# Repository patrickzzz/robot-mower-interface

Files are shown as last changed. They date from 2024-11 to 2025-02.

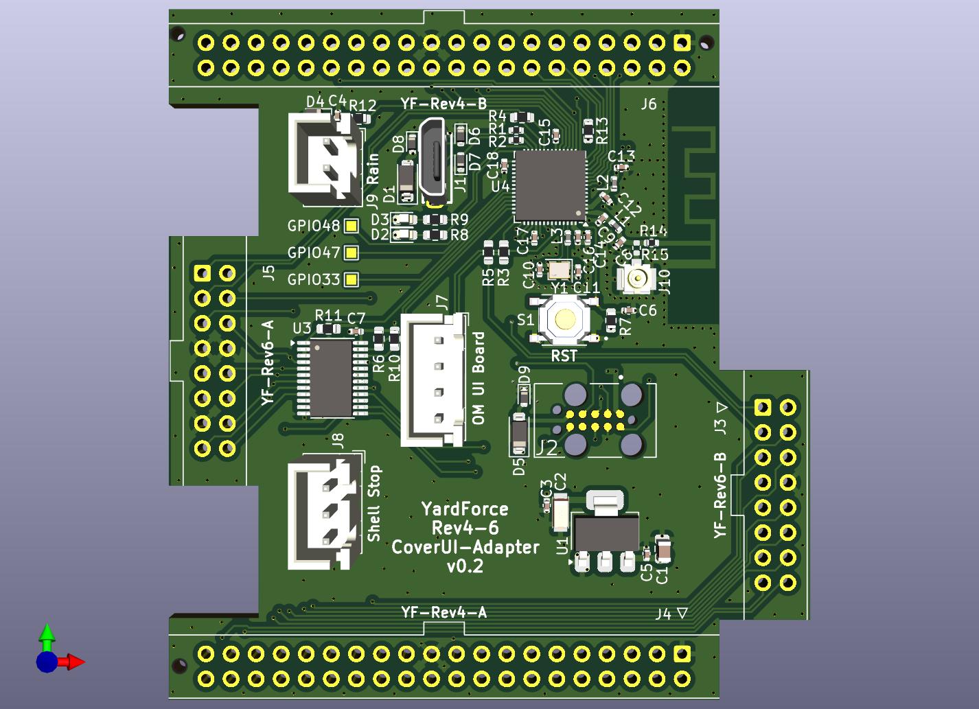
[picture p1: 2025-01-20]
hardware/yardforce/YF-Rev4-6-Adapter.jpg

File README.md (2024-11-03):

# Robot Mower Interface

## Overview
This project provides an interface for controlling and managing a robot mower.

Initially this is done for a Ferrex R800Easy+ robot mower (meaning, it will be probably easily adaptable to other models from Ferrex, Yard Force (Yardforce), Garden Feelings and so on). 

## Original Goals
- The mower lacks the possibility to mow less than 4 hours a day. Also it has no app to control it (other models may have an app, but only closed source). These are the main reasons for this project.
- The main goal is a personal use case. There still might be errors in the project and/or in the documentation.

## Features
- **Control**: Execute Start, Home, Stop, and Lock on the mower.
- **Configuration**: Configure Wi-Fi settings (either connected to a Wifi, or as Access Point).
- **Scheduling**: Set mowing schedules.
- **Status**: View mower status
- **Logs**: See logs from the mower
- **API** Access all features via API
- **Web Interface** Access all features via a web interface
- **OTA Updates** Update the firmware and filesystem of the mower interface over the air (OTA) in Webinterface or API Endpoint.

## Demo of first running version
Demo (https://www.youtube.com/watch?v=VGW71knz1Dk)

## License
This project is licensed under the Creative Commons Zero v1.0 Universal (CC0 1.0) - see the [LICENSE](LICENSE) file for details.

It's important to note that the original firmware of the mower is not open source, and this project is not affiliated with the manufacturer.
The original firmware of the mower is not changed in any way, but the warranty of the mower will be voided modifying the mower in this way.
I am not responsible for any damage to the mower or any other device.

## API Endpoint Documentation

### 1. `/start`
- **Method:** `POST`
- **Description:** Starts the mower.
- **Parameters:** None
- **Response:** `200 OK` if successful

### 2. `/home`
- **Method:** `POST`
- **Description:** Sends the mower back to the charging station.
- **Parameters:** None
- **Response:** `200 OK` if successful

### 3. `/stop`
- **Method:** `POST`
- **Description:** Stops the mower.
- **Parameters:** None
- **Response:** `200 OK` if successful

### 4. `/lock`
- **Method:** `POST`
- **Description:** Locks the mower.
- **Parameters:** None
- **Response:** `200 OK` if successful

### 5. `/unlock`
- **Method:** `POST`
- **Description:** Unlocks the mower.
- **Parameters:** None
- **Response:** `200 OK` if successful

### 6. `/status`
- **Method:** `GET`
- **Description:** Returns the current status of the mower.
- **Parameters:** None
- **Response:** JSON object with the following fields:
    - `date`: Current date on the mower
    - `time`: Current time on the mower
    - `isCharging`: Charging status
    - `isLocked`: Lock status
    - `isEmergency`: Emergency status
    - `isIdle`: Idle status
    - `isAccessPoint`: Access Point mode status
    - `hostname`: Hostname of the mower
    - `ssid`: Current WiFi SSID
    - `ip`: IP address of the mower
    - `mowingPlanActive`: Indicates if the mowing plan is active

### 7. `/mowing-plan`
- **Method:** `GET`
- **Description:** Retrieves the current mowing plan.
- **Parameters:** None
- **Response:** JSON file of the mowing plan if exists, or `204 No Content` if not found

### 8. `/mowing-plan`
- **Method:** `POST`
- **Description:** Sets a new mowing plan.
- **Payload:** JSON object with the following fields:
    - `customMowingPlanActive` (boolean): Activates or deactivates the custom mowing plan
    - `days` (array of booleans): Specifies active days (Mon-Sun)
    - `planTimeStart` (string): Mowing start time (e.g., `"09:00"`)
    - `planTimeEnd` (string): Mowing end time (e.g., `"17:00"`)
- **Response:** `200 OK` if successful, `400 Bad Request` if parameters are missing

### 9. `/wifis`
- **Method:** `GET`
- **Description:** Returns a list of available WiFi networks.
- **Parameters:** None
- **Response:** JSON array with SSIDs of the detected networks

### 10. `/wifi`
- **Method:** `POST`
- **Description:** Sets the WiFi credentials for the mower to connect to.
- **Payload:** JSON object with the following fields:
    - `ssid` (string): WiFi SSID
    - `password` (string): WiFi password
- **Response:** `200 OK` if successful, `400 Bad Request` if parameters are missing

### 11. `/date-time`
- **Method:** `POST`
- **Description:** Sets the date and time on the mower.
- **Payload:** JSON object with the following fields:
    - `date` (string): Date in the format `YYYY-MM-DD`
    - `time` (string): Time in the format `HH:MM`
- **Response:** `200 OK` if successful, `400 Bad Request` if parameters are missing

### 12. `/update`
- **Method:** `POST`
- **Description:** Allows for simultaneous upload and update of both firmware and filesystem files on the device. This endpoint manages both types of updates, determining the file type based on the filename.
- **Payload:** Multipart form-data with up to two files:
  - `firmware.bin`: Firmware binary file for updating the main program.
  - `filesystem.bin`: Filesystem binary file (e.g., SPIFFS) for updating the file system.
- **Response:**
  - **`200 OK`**: Returns `"Update Success!"` if the upload and update process are successful for both files.
  - **`500 Internal Server Error`**: Returns `"Update Failed!"` if an error occurs during either update.
- **Usage Notes:**
  - **File Recognition**: The update type is determined by the filename—`firmware.bin` for firmware updates and `filesystem.bin` for filesystem updates.
  - **Restart**: Upon successful updates, the device automatically restarts to apply changes.

## Needed parts
- Ferrex R800Easy+ robot mower (or similar)
- ESP32 (e.g., ESP32 DevKitC)
- USB cable
- DC-DC step-down converter (~32V -> 5V)

## Software Installation Instructions
Follow these steps to install the mower control software on your ESP32:

- **Connect** your ESP32 to your computer via USB.
- **Clone** this Repository
- **Install** PlatformIO (if not installed)
- **Upload the File System:** In the project/backend directory, upload the filesystem to the ESP32 by running:
  ```bash
  pio run --target uploadfs
  ```
- **Upload the Firmware:** In the project/backend directory, upload the firmware to the ESP32:
  ```bash
  pio run --target upload
  ```

- **Verify Installation:** Once complete, the ESP32 should be ready to run with the mower control software, creating a Wifi Access Point with SSID "Robot Mower" and password: "MowerInterface".
- **While still connected with USB to the ESP32, open a Serial Monitor** and you should see the IP address of the ESP32. Use this IP address to access the web interface.
  ```bash
  pio device monitor
  ```

## Hardware Installation Instructions
- For now the ESP32 has to be powered from the mainboard, and several pins of the ESP32 have to be connected to the Cover-User-Interface-Board (CoverUI).
- The power (24V) will come from red J18 connector. This is constant and is not powered down in idle mode. Connect it to the DC-DC step-down converter and set this to 5V.
- The ESP32 will be powered from the 5V output of the DC-DC step-down converter.
- The Stop1 (J8) cable on the main board for now has to be disconnected. The bottom Stop button of the mower will not work anymore. The top Stop button will still work.
- The connection of the pins of the ESP32 will for now not be described here, but hopefully can be seen in the following pictures, or derived from the code.

## Photos





## Thanks To
Special thanks to the following projects and contributors:
- **[apehaenger/CoverUI](https://github.com/apehaenger/CoverUI)** — for extensive help on the mower and detailed documentation.
- **[ClemensElflein/OpenMower](https://github.com/ClemensElflein/OpenMower)** — for the inspiration behind this project.
- **[cedbossneo/Mowgli](https://github.com/cedbossneo/Mowgli)** — for mainboard documentation and insights.

And a big thanks to all contributors from these projects, as well as the developers of the hardware and software used in this project.

Last but not least, to my girlfriend and family for their patience and support during my development time.

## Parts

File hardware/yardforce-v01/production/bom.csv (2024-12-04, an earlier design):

Designator | Footprint | Quantity | Value | LCSC Part #
C1, C2 | 0603 | 2 | 10uF | C19702
C10, C11 | 0402 | 2 | 10pF | C32949
C12, C15, C16, C17, C18, C3, C4, C7 | 0402 | 8 | .1uF | C1525
C14, C6 | 0402 | 2 | 1uF | C52923
C9 | 0402 | 1 | 0.8pF | C5448872
D1 | D_SOD-123 | 1 | D_Schottky | C82288
D2 | 0603 | 1 | LED GREEN | C12624
D3 | 0603 | 1 | LED RED | C2286
D4 | D_SOD-323 | 1 | PDZ3.3B,115 | C426855
J1 | USB_Micro-B_Wuerth_614105150721_Vertical | 1 | USB_OTG | C668588
J7 | JST_XH_B4B-XH-A_1x04_P2.50mm_Vertical | 1 | OM UI Board | C144395
J8 | JST_XH_B3B-XH-A_1x03_P2.50mm_Vertical | 1 | Shell Stop | C144394
J9 | JST_XH_B2B-XH-A_1x02_P2.50mm_Vertical | 1 | Rain | C2910525
L1 | 0402 | 1 | 3.9nH | C370223
L2 | 0402 | 1 | 2.0nH | C963978
L3 | 0402 | 1 | 24nH | C401493
R1, R2 | 0402 | 2 | 0 | C17168
R10, R11, R12, R6, R7 | 0603 | 5 | 10k | C25804
R3, R4, R5 | 0603 | 3 | 22 | C23345
R8 | 0603 | 1 | 200 | C8218
R9 | 0603 | 1 | 220 | C22962
S1 | SW_TS-1187A-B-A-B | 1 | RST | C318884
U1 | SOT-223-3_TabPin2 | 1 | AMS1117-3.3 | C6186
U3 | TSSOP-24_4.4x7.8mm_P0.65mm | 1 | TCA9555PWR | C465732
U4 | QFN-56-1EP_7x7mm_P0.4mm_EP4x4mm_ThermalVias | 1 | ESP32-S3-FH4R2 | C3013940
Y1 | Crystal_SMD_2016-4Pin_2.0x1.6mm | 1 | 40MHz 10.5pF ±10ppm | C18209006

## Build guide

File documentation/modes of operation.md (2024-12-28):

## Possible operation modes

### Mainboard / CoverUI matrix of possible adapter connection variants

| Mainboard \ CoverUI | YF-Rev4-A\|B | YF-Rev6-A<br>via UART1[^1] | YF-Rev6-B<br>via UART2[^2] |
|---|:---:|:---:|:---:|
| **OM UI Board**<br>via UART0[^3] | ✔ | ✔ | ✔ |
| **YF-Rev4-A\|B**<br>No UART, read LED states  | ✔ | ✔ | ✔ |
| **YF-Rev6-A**<br>via UART1[^1] | ✔ | ✘ | ✔ |
| **YF-Rev6-B**<br>via UART2[^2] | ✔ | ✔ | ✘ |

[^1]: UART1 via TXD1 = GPIO17, RXD1 = GPIO18
[^2]: UART2 via TXDX = GPIO37, RXDX = GPIO38
[^3]: UART0 via TXD0 = GPIO43, RXD0 = GPIO44

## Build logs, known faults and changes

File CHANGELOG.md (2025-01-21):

# Changelog

All notable changes to this project are documented in this file.

## [0.3.2]
### Changed
- Don't truncate logs on every startup

### Fixed
- Correct loading of mowing plan on boot up

## [0.3.1]
### Changed
- Visualize Log message in webinterface as mono spaced text
- Load mowing plan on boot up again

## [0.3.0]
### Added
- Ability to update the firmware+filesystem of the mower interface over the air (OTA) in Webinterface or API Endpoint.

## [0.2.2]
### Added
- Automatically reconnect to Wifi if connection is lost

## [0.2.1]
### Changed
- Forced serving of html+js gzipped
- Increased wdt to 60s for handling bigger requests (hopefully not needed)

## [0.2.0]
### Added
- Documentation added.

### Changed
- Changed license from MIT to CC0 1.0 Universal.
- Minor improvements in frontend.
- Backend code restructuring.
- WiFi scanning now asynchronous.

### Fixed
- Issue with logging (log file truncation error corrected).
- Time setting now expects new JSON payload.

## [0.1.0]
### Initial Release
- Initial version of the project.

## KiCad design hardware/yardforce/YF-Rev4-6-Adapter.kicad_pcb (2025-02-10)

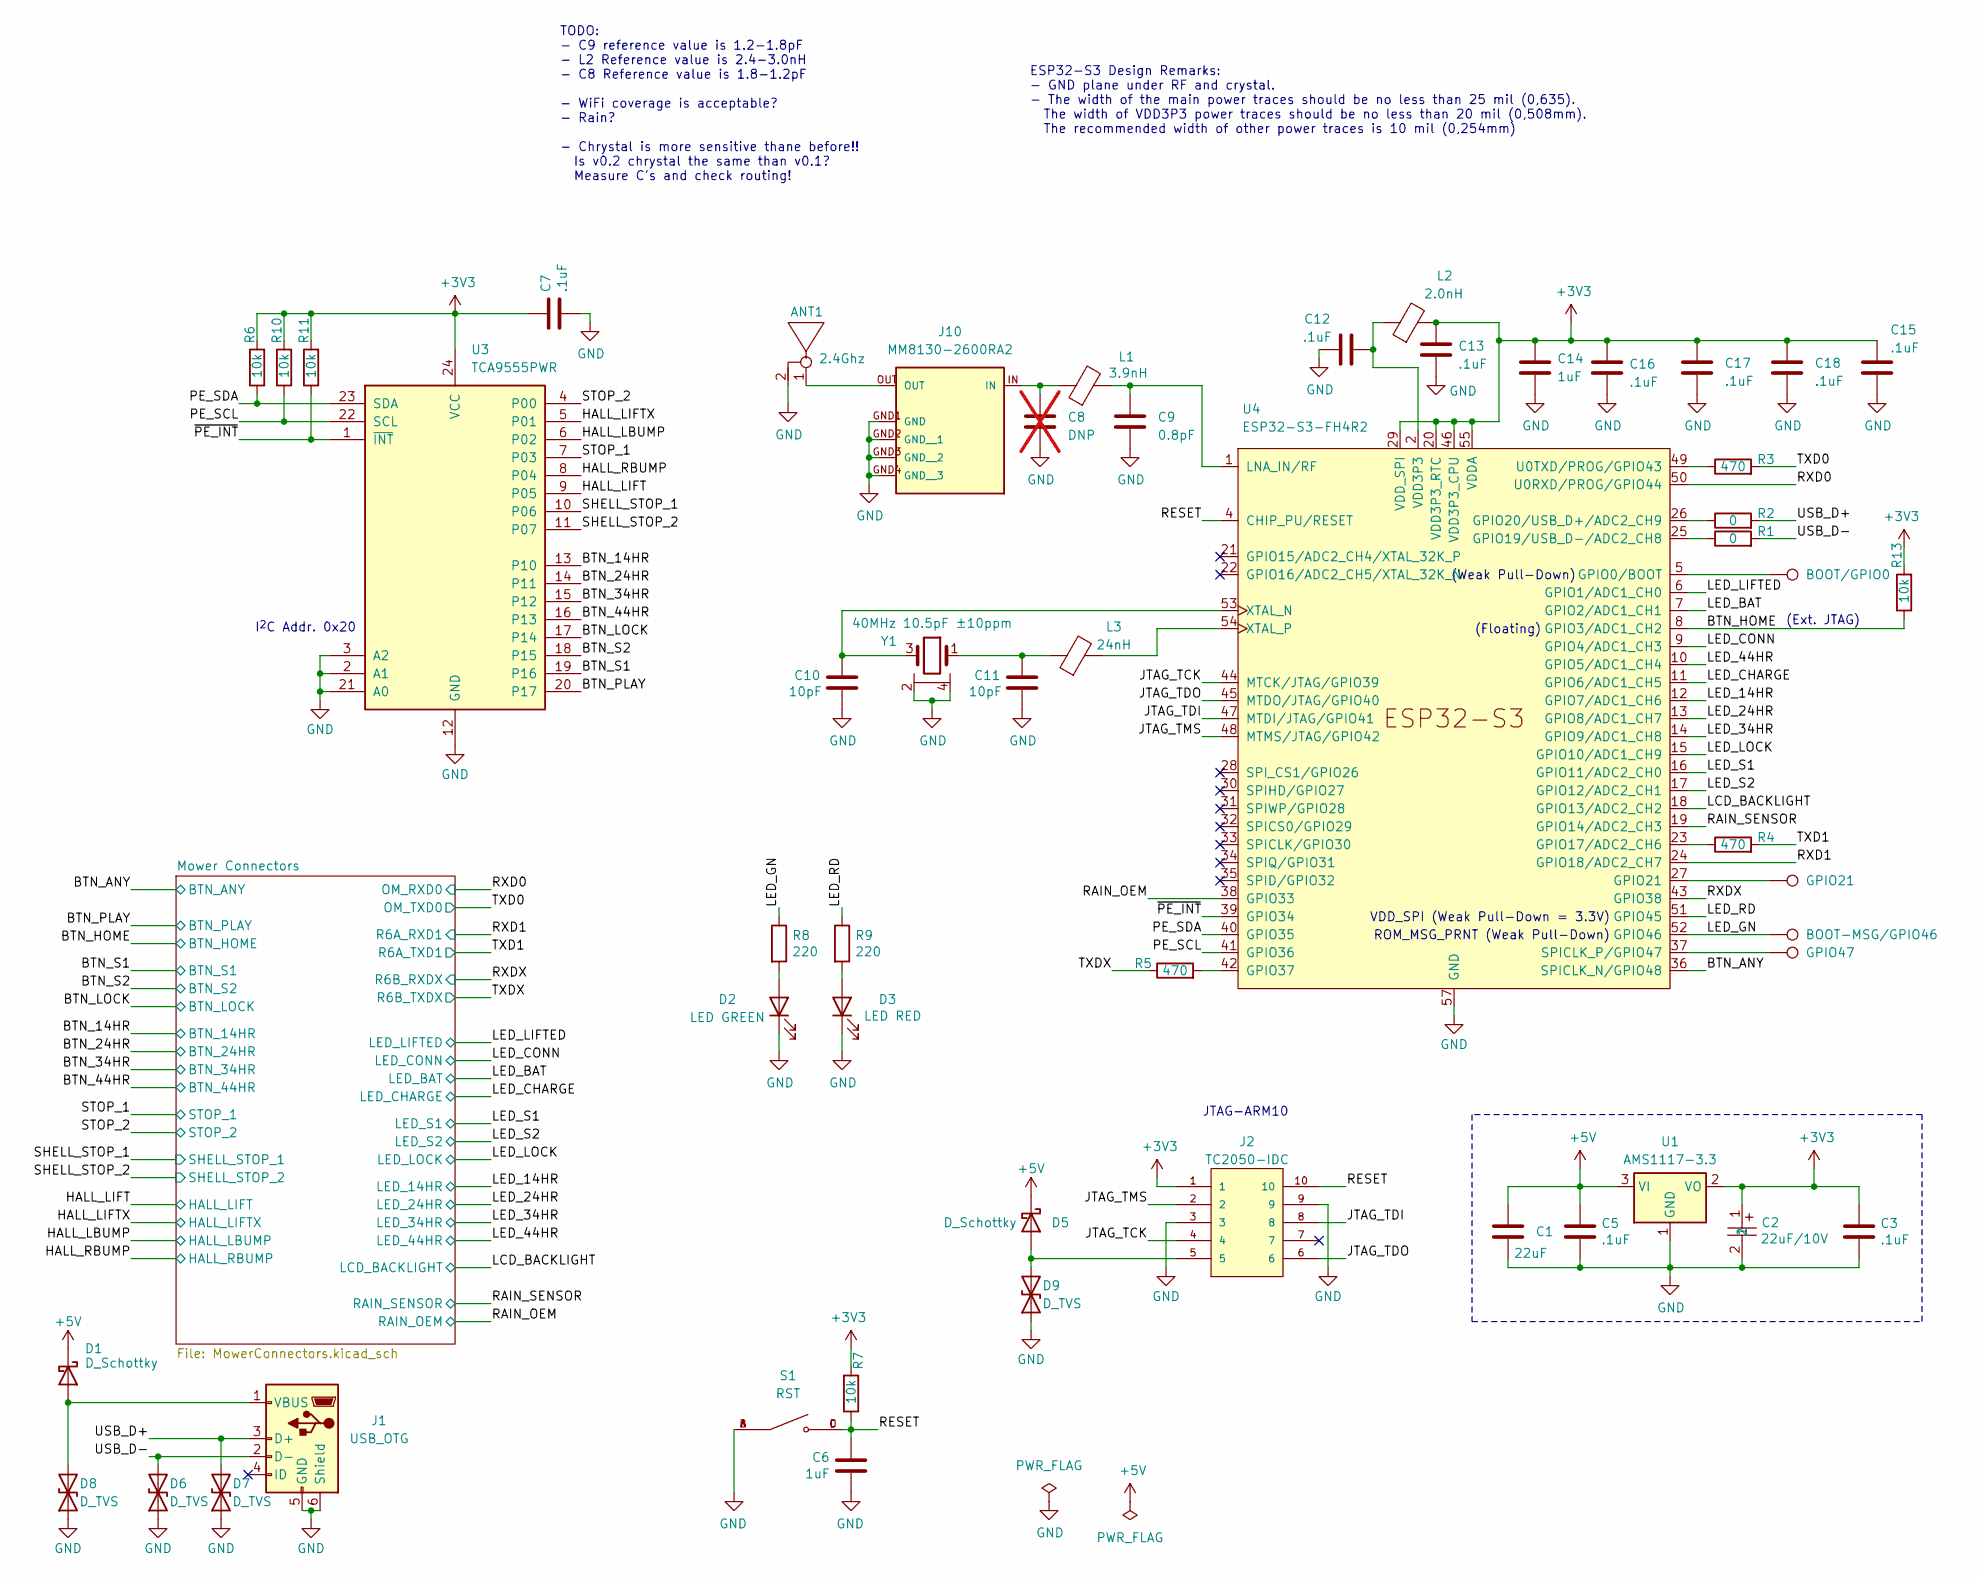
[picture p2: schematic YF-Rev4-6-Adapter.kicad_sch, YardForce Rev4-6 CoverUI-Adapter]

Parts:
ANT1: 2.4Ghz; PCB_Antenna_2.4GHz_Left
BOOT-MSG/GPIO46: TestPoint; TestPoint_Pad_1.0x1.0mm
BOOT/GPIO0: TestPoint; TestPoint_Pad_1.0x1.0mm
C1: 22uF; C_0805_2012Metric; LCSC C45783
C2: 22uF/10V; CASE-A_3216; LCSC C129272
C3, C5, C7, C12, C13, C15, C16, C17, C18: .1uF; C_0402_1005Metric; LCSC C1525
C6, C14: 1uF; C_0402_1005Metric; LCSC C52923
C8: DNP; C_0402_1005Metric; not fitted
C9: 0.8pF; C_0402_1005Metric; LCSC C5448872
C10, C11: 10pF; C_0402_1005Metric; MFR Part 0402CG140J500NT; LCSC C32949
D1, D5: D_Schottky; D_SOD-123; Part Number 1N5819HW-7-F; LCSC C82544
D2: LED GREEN; LED_0603_1608Metric; Part Number LTST-C191KGKT; Digikey 160-1446-1-ND
D3: LED RED; LED_0603_1608Metric; Part Number LTST-C191KRKT; Digikey 160-1447-1-ND
D6, D7, D8, D9: D_TVS; D_SOD-523; Part-Nr LESD5D5.0CT1G; LCSC C5449097
GPIO21, GPIO47: TestPoint; TestPoint_Pad_1.0x1.0mm
J1: USB_OTG; MINI-USB-SMD_U255-051N-4BH70-XS; LCSC C437033
J2: TC2050-IDC; TAG-CONNECT_TC2050-IDC; PARTREV A
J10: MM8130-2600RA2; MURATA_MM8130-2600RA2; LCSC C91633
L1: 3.9nH; L_0402_1005Metric; LCSC C370223
L2: 2.0nH; L_0402_1005Metric; LCSC C963978
L3: 24nH; L_0402_1005Metric; MFR Part SDCL1005C24NJTDF; LCSC C401493
R1, R2: 0; R_0402_1005Metric; LCSC C17168
R3, R4, R5: 470; R_0603_1608Metric; LCSC C23179
R6, R7, R10, R11, R13: 10k; R_0603_1608Metric; LCSC C25804
R8, R9: 220; R_0603_1608Metric; LCSC C22962
S1: RST; SW_TS-1187A-B-A-B; PARTREV A0; LCSC C318884
U1: AMS1117-3.3; SOT-223-3_TabPin2; LCSC C6186
U3: TCA9555PWR; TSSOP-24_4.4x7.8mm_P0.65mm; LCSC C465732
U4: ESP32-S3-FH4R2; QFN-56-1EP_7x7mm_P0.4mm_EP4x4mm_ThermalVias; LCSC C3013940
Y1: 40MHz 10.5pF ±10ppm; Crystal_SMD_2016-4Pin_2.0x1.6mm; MF Part K2B4000010510; LCSC C18209006

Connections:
+3V3: C2.1, C3.1, C7.1, C13.1, C14.1, C15.1, C16.1, C17.1, C18.1, J2.1, L2.2, R6.2, R7.2, R10.2, R11.2, R13.2, U1.2 (VO), U3.24 (VCC), U4.20 (VDD3P3_RTC), U4.29 (VDD_SPI), U4.46 (VDD3P3_CPU), U4.55 (VDDA), U4.56 (VDDA); also elsewhere on the board
+5V: C1.1, C5.1, D1.1 (K), D5.1 (K), U1.3 (VI); also elsewhere on the board
/BTN_14HR: U3.13 (P10); also elsewhere on the board
/BTN_24HR: U3.14 (P11); also elsewhere on the board
/BTN_34HR: U3.15 (P12); also elsewhere on the board
/BTN_44HR: U3.16 (P13); also elsewhere on the board
/BTN_ANY: U4.36 (SPICLK_N/GPIO48); also elsewhere on the board
/BTN_HOME: R13.1, U4.8 (GPIO3/ADC1_CH2); also elsewhere on the board
/BTN_LOCK: U3.17 (P14); also elsewhere on the board
/BTN_PLAY: U3.20 (P17); also elsewhere on the board
/BTN_S1: U3.19 (P16); also elsewhere on the board
/BTN_S2: U3.18 (P15); also elsewhere on the board
/HALL_LBUMP: U3.6 (P02); also elsewhere on the board
/HALL_LIFT: U3.9 (P05); also elsewhere on the board
/HALL_LIFTX: U3.5 (P01); also elsewhere on the board
/HALL_RBUMP: U3.8 (P04); also elsewhere on the board
/JTAG_TCK: J2.4, U4.44 (MTCK/JTAG/GPIO39)
/JTAG_TDI: J2.8, U4.47 (MTDI/JTAG/GPIO41)
/JTAG_TDO: J2.6, U4.45 (MTDO/JTAG/GPIO40)
/JTAG_TMS: J2.2, U4.48 (MTMS/JTAG/GPIO42)
/LCD_BACKLIGHT: U4.18 (GPIO13/ADC2_CH2); also elsewhere on the board
/LED_14HR: U4.12 (GPIO7/ADC1_CH6); also elsewhere on the board
/LED_24HR: U4.13 (GPIO8/ADC1_CH7); also elsewhere on the board
/LED_34HR: U4.14 (GPIO9/ADC1_CH8); also elsewhere on the board
/LED_44HR: U4.10 (GPIO5/ADC1_CH4); also elsewhere on the board
/LED_BAT: U4.7 (GPIO2/ADC1_CH1); also elsewhere on the board
/LED_CHARGE: U4.11 (GPIO6/ADC1_CH5); also elsewhere on the board
/LED_CONN: U4.9 (GPIO4/ADC1_CH3); also elsewhere on the board
/LED_GN: BOOT-MSG/GPIO46.1, R8.1, U4.52 (GPIO46)
/LED_LIFTED: U4.6 (GPIO1/ADC1_CH0); also elsewhere on the board
/LED_LOCK: U4.15 (GPIO10/ADC1_CH9); also elsewhere on the board
/LED_RD: R9.1, U4.51 (GPIO45)
/LED_S1: U4.16 (GPIO11/ADC2_CH0); also elsewhere on the board
/LED_S2: U4.17 (GPIO12/ADC2_CH1); also elsewhere on the board
/PE_SCL: R10.1, U3.22 (SCL), U4.41 (GPIO36)
/PE_SDA: R6.1, U3.23 (SDA), U4.40 (GPIO35)
/RAIN_OEM: U4.38 (GPIO33); also elsewhere on the board
/RAIN_SENSOR: U4.19 (GPIO14/ADC2_CH3); also elsewhere on the board
/RESET: C6.1, J2.10, R7.1, S1.C, S1.D, U4.4 (CHIP_PU/RESET)
/RXD0: U4.50 (U0RXD/PROG/GPIO44); also elsewhere on the board
/RXD1: U4.24 (GPIO18/ADC2_CH7); also elsewhere on the board
/RXDX: U4.43 (GPIO38); also elsewhere on the board
/SHELL_STOP_1: U3.10 (P06); also elsewhere on the board
/SHELL_STOP_2: U3.11 (P07); also elsewhere on the board
/STOP_1: U3.7 (P03); also elsewhere on the board
/STOP_2: U3.4 (P00); also elsewhere on the board
/TXD0: R3.2; also elsewhere on the board
/TXD1: R4.2; also elsewhere on the board
/TXDX: R5.1; also elsewhere on the board
/USB_D+: D7.2 (A2), J1.3 (D+), R2.2
/USB_D-: D6.2 (A2), J1.2 (D-), R1.2
/~PE_INT: R11.1, U3.1 (~INT), U4.39 (GPIO34)
GND: ANT1.2, C1.2, C2.2, C3.2, C5.2, C6.2, C7.2, C8.2, C9.2, C10.2, C11.2, C12.1, C13.2, C14.2, C15.2, C16.2, C17.2, C18.2, D2.1 (K), D3.1 (K), D6.1 (A1), D7.1 (A1), D8.1 (A1), D9.1 (A1), J1.5 (GND), J1.6 (Shield), J2.3, J2.9, J10.GND1 (GND), J10.GND2 (GND__1), J10.GND3 (GND__2), J10.GND4 (GND__3), S1.A, S1.B, U1.1 (GND), U3.2 (A1), U3.3 (A2), U3.12 (GND), U3.21 (A0), U4.57 (GND), Y1.2, Y1.4; also elsewhere on the board
unnamed: ANT1.1, J10.OUT
unnamed: C8.1, J10.IN, L1.1
unnamed: C11.1, L3.1, Y1.1
unnamed: D1.2 (A), D8.2 (A2), J1.1 (VBUS)
unnamed: D2.2 (A), R8.2
unnamed: D3.2 (A), R9.2
unnamed: D5.2 (A), D9.2 (A2), J2.5
unnamed: BOOT/GPIO0.1, U4.5 (GPIO0/BOOT)
unnamed: R4.1, U4.23 (GPIO17/ADC2_CH6)
unnamed: R1.1, U4.25 (GPIO19/USB_D-/ADC2_CH8)
unnamed: R2.1, U4.26 (GPIO20/USB_D+/ADC2_CH9)
unnamed: GPIO21.1, U4.27 (GPIO21)
unnamed: R5.2, U4.42 (GPIO37)
unnamed: C9.1, L1.2, U4.1 (LNA_IN/RF)
unnamed: GPIO47.1, U4.37 (SPICLK_P/GPIO47)
unnamed: R3.1, U4.49 (U0TXD/PROG/GPIO43)
unnamed: C10.1, U4.53 (XTAL_N), Y1.3
unnamed: L3.2, U4.54 (XTAL_P)
VDD3P3: C12.2, L2.1, U4.2 (VDD3P3), U4.3 (VDD3P3)

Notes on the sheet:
(Floating)
ESP32-S3 Design Remarks: - GND plane under RF and crystal. - The width of the main power traces should be no less than 25 mil (0,635). The width of VDD3P3 power traces should be no less than 20 mil (0,508mm). The recommended width of other power traces is 10 mil (0,254mm)
ROM_MSG_PRNT (Weak Pull-Down)
(Weak Pull-Down)
JTAG-ARM10
(Ext. JTAG)
VDD_SPI (Weak Pull-Down = 3.3V)
I^{2}C Addr. 0x20
TODO: - C9 reference value is 1.2-1.8pF - L2 Reference value is 2.4-3.0nH - C8 Reference value is 1.8-1.2pF - WiFi coverage is acceptable? - Rain? - Chrystal is more sensitive thane before!! Is v0.2 chrystal the same than v0.1? Measure C's and check routing!

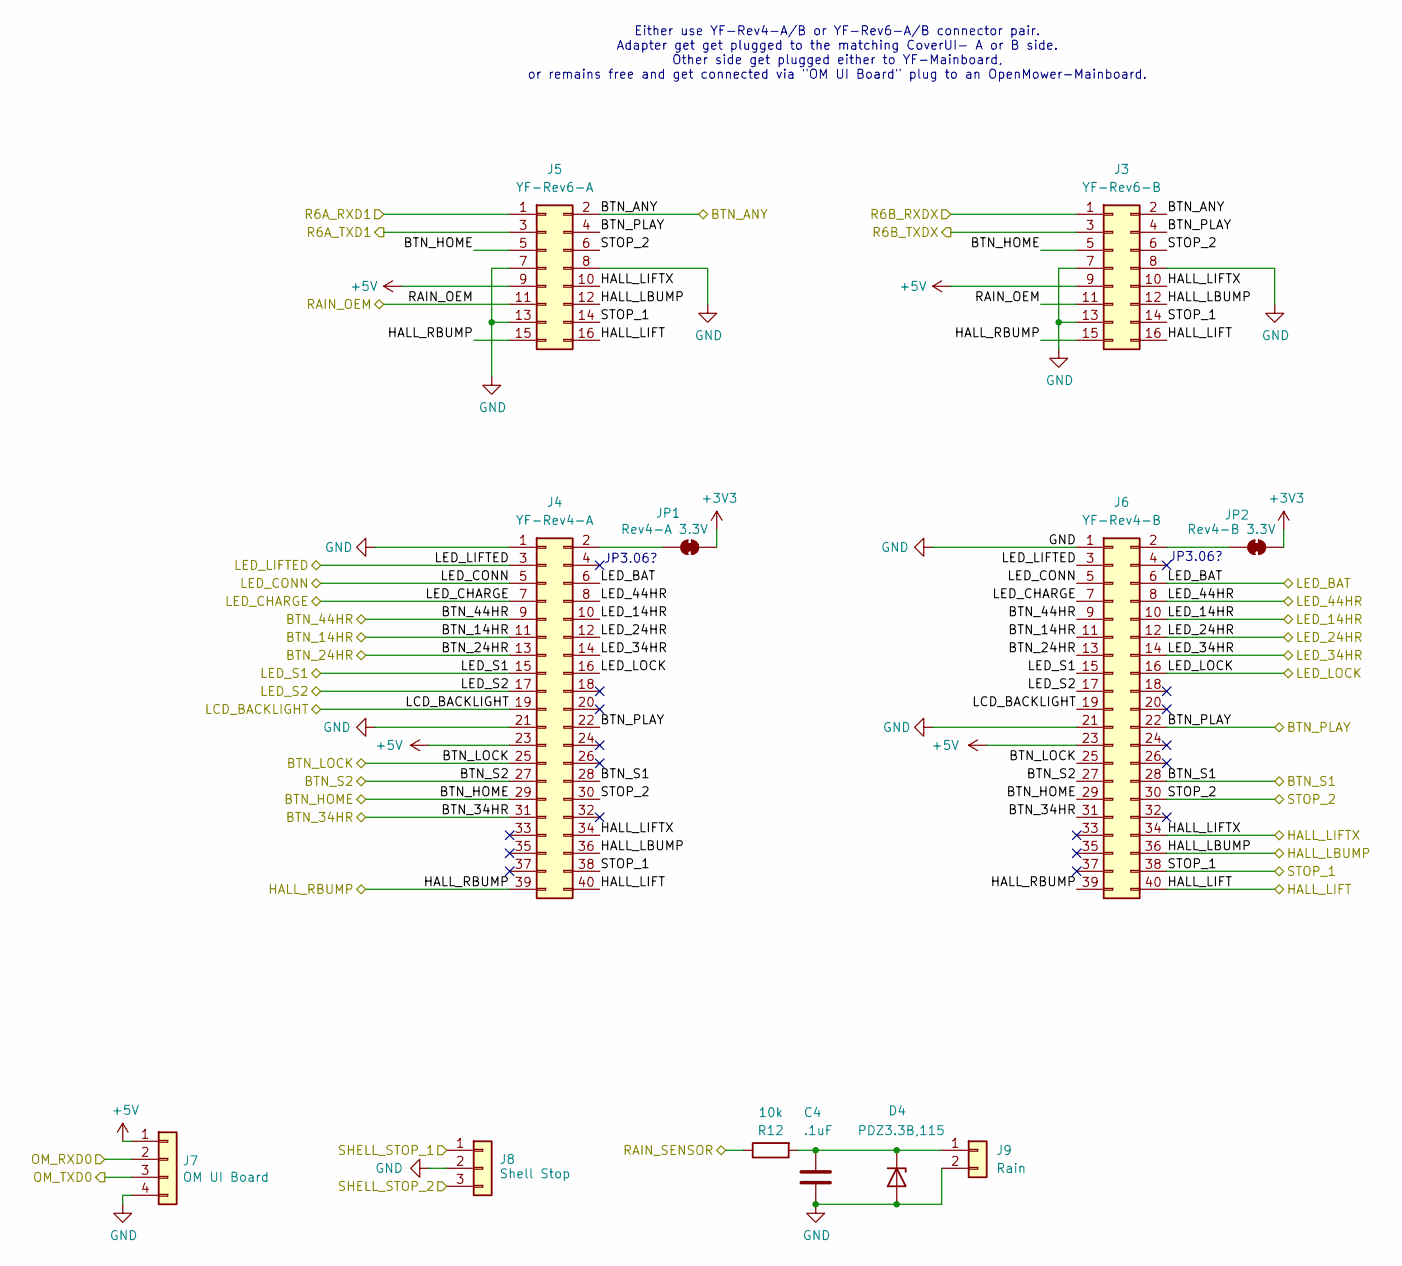
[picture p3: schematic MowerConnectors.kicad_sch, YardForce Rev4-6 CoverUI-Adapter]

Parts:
C4: .1uF; C_0402_1005Metric; JLC C307331
D4: PDZ3.3B,115; D_SOD-323; JLC C426855
J3: YF-Rev6-B; IDC-Hybrid_2x08_P2.54mm_Latch_Vertical; DigiKey S9196-ND
J4: YF-Rev4-A; IDC-Hybrid_2x20_P2.54mm_Latch_Vertical; DigiKey SFH11-PBPC-D20-ST-BK
J5: YF-Rev6-A; IDC-Hybrid_2x08_P2.54mm_Latch_Vertical; DigiKey S9196-ND
J6: YF-Rev4-B; IDC-Hybrid_2x20_P2.54mm_Latch_Vertical; DigiKey SFH11-PBPC-D20-ST-BK
J7: OM UI Board; JST_XH_B4B-XH-A_1x04_P2.50mm_Vertical; Part Number B4B-XH-A(LF)(SN); Digikey 455-2249-ND
J8: Shell Stop; JST_XH_B3B-XH-A_1x03_P2.50mm_Vertical; Part Number B3B-XH-A(LF)(SN); LCSC C144394
J9: Rain; JST_XH_B2B-XH-A_1x02_P2.50mm_Vertical; Part Number ZX-XH2.54-2PZZ; LCSC C7429632
JP1: Rev4-A 3.3V; SolderJumper-2_P1.3mm_Bridged_RoundedPad1.0x1.5mm
JP2: Rev4-B 3.3V; SolderJumper-2_P1.3mm_Bridged_RoundedPad1.0x1.5mm
R12: 10k; R_0603_1608Metric; JLC C25744

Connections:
+3V3: JP1.2 (B), JP2.2 (B); also elsewhere on the board
+5V: J3.9, J4.23, J5.9, J6.23, J7.1; also elsewhere on the board
/BTN_14HR: J4.11, J6.11; also elsewhere on the board
/BTN_24HR: J4.13, J6.13; also elsewhere on the board
/BTN_34HR: J4.31, J6.31; also elsewhere on the board
/BTN_44HR: J4.9, J6.9; also elsewhere on the board
/BTN_ANY: J3.2, J5.2; also elsewhere on the board
/BTN_HOME: J3.5, J4.29, J5.5, J6.29; also elsewhere on the board
/BTN_LOCK: J4.25, J6.25; also elsewhere on the board
/BTN_PLAY: J3.4, J4.22, J5.4, J6.22; also elsewhere on the board
/BTN_S1: J4.28, J6.28; also elsewhere on the board
/BTN_S2: J4.27, J6.27; also elsewhere on the board
/HALL_LBUMP: J3.12, J4.36, J5.12, J6.36; also elsewhere on the board
/HALL_LIFT: J3.16, J4.40, J5.16, J6.40; also elsewhere on the board
/HALL_LIFTX: J3.10, J4.34, J5.10, J6.34; also elsewhere on the board
/HALL_RBUMP: J3.15, J4.39, J5.15, J6.39; also elsewhere on the board
/LCD_BACKLIGHT: J4.19, J6.19; also elsewhere on the board
/LED_14HR: J4.10, J6.10; also elsewhere on the board
/LED_24HR: J4.12, J6.12; also elsewhere on the board
/LED_34HR: J4.14, J6.14; also elsewhere on the board
/LED_44HR: J4.8, J6.8; also elsewhere on the board
/LED_BAT: J4.6, J6.6; also elsewhere on the board
/LED_CHARGE: J4.7, J6.7; also elsewhere on the board
/LED_CONN: J4.5, J6.5; also elsewhere on the board
/LED_LIFTED: J4.3, J6.3; also elsewhere on the board
/LED_LOCK: J4.16, J6.16; also elsewhere on the board
/LED_S1: J4.15, J6.15; also elsewhere on the board
/LED_S2: J4.17, J6.17; also elsewhere on the board
/RAIN_OEM: J3.11, J5.11; also elsewhere on the board
/RAIN_SENSOR: R12.1; also elsewhere on the board
/RXD0: J7.2; also elsewhere on the board
/RXD1: J5.1; also elsewhere on the board
/RXDX: J3.1; also elsewhere on the board
/SHELL_STOP_1: J8.1; also elsewhere on the board
/SHELL_STOP_2: J8.3; also elsewhere on the board
/STOP_1: J3.14, J4.38, J5.14, J6.38; also elsewhere on the board
/STOP_2: J3.6, J4.30, J5.6, J6.30; also elsewhere on the board
/TXD0: J7.3; also elsewhere on the board
/TXD1: J5.3; also elsewhere on the board
/TXDX: J3.3; also elsewhere on the board
GND: C4.2, D4.2 (A), J3.7, J3.8, J3.13, J4.1, J4.21, J5.7, J5.8, J5.13, J6.1, J6.21, J7.4, J8.2, J9.2; also elsewhere on the board
unnamed: C4.1, D4.1 (K), J9.1, R12.2
unnamed: J4.2, JP1.1 (A)
unnamed: J6.2, JP2.1 (A)

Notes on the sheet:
JP3.06?
Either use YF-Rev4-A/B or YF-Rev6-A/B connector pair. Adapter get get plugged to the matching CoverUI- A or B side. Other side get plugged either to YF-Mainboard, or remains free and get connected via "OM UI Board" plug to an OpenMower-Mainboard.

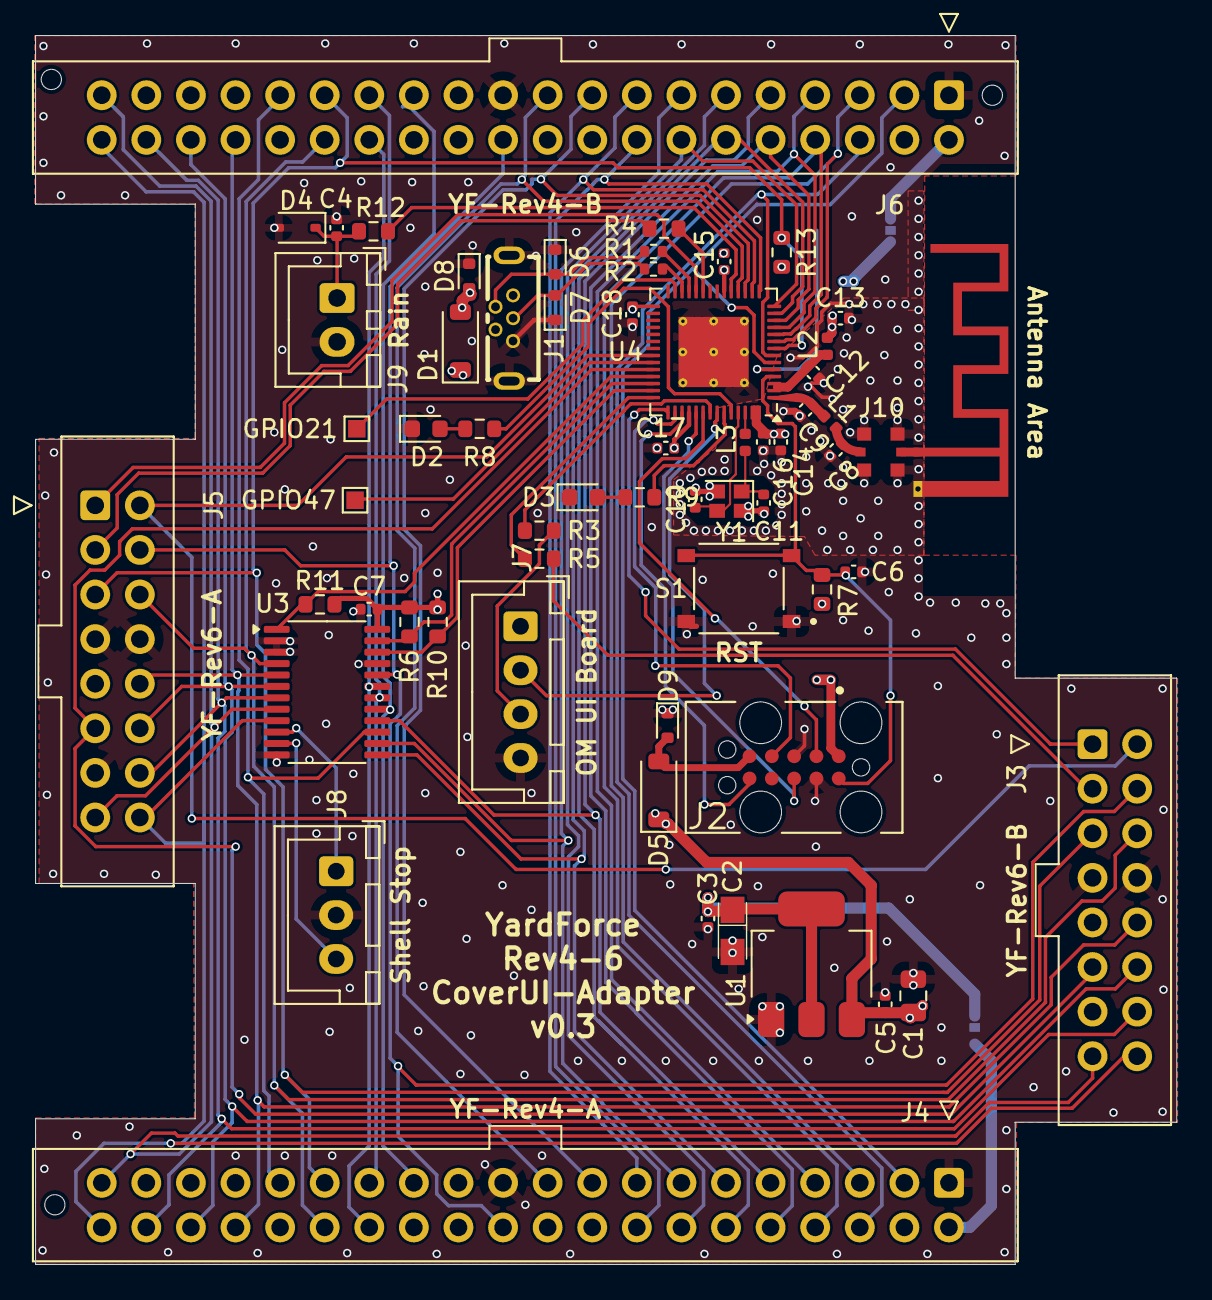
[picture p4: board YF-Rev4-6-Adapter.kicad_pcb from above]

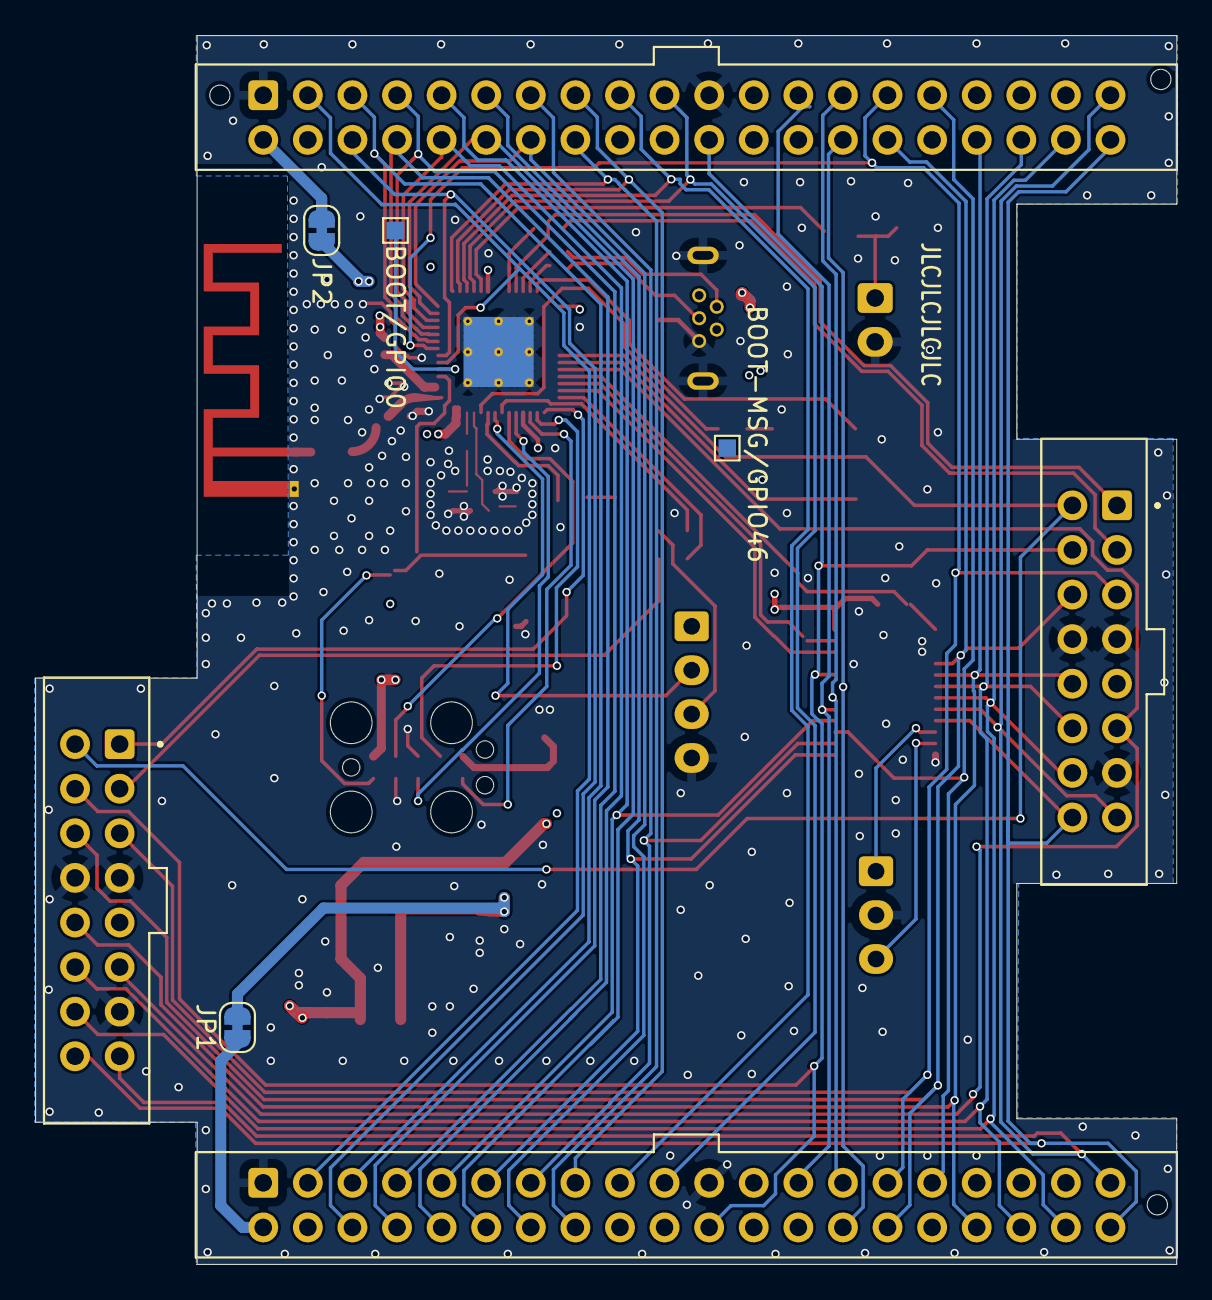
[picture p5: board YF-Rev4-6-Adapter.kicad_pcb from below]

Board: 4 copper layers, 65.0 x 70.0 mm, 65 parts (4 on the bottom side), 75 nets.

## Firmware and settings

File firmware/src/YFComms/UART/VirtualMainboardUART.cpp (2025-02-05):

#include "VirtualMainboardUART.hpp"
#include "esp_log.h"
#include <cstring>
#include <freertos/FreeRTOS.h>
#include <freertos/task.h>

namespace YFComms {
    const VirtualMainboardUART::HandshakeMessageResponsePair VirtualMainboardUART::handshakeMessageResponses[] = {
        {{0x55, 0xAA, 0x03, 0x40, 0x01, 0x00, 0x43}, {0x55, 0xAA, 0x02, 0xFF, 0xFF, 0xFF}, 7, 6, false},
        {{0x55, 0xAA, 0x02, 0xFF, 0xFF, 0xFF}, {0x55, 0xAA, 0x02, 0xFF, 0xFE, 0xFE}, 6, 6, false},
        {{0x55, 0xAA, 0x02, 0xFF, 0xFE, 0xFE}, {0x55, 0xAA, 0x05, 0xFF, 0xFD, 0x06, 0x50, 0x20, 0x76}, 6, 9, false},
        {{0x55, 0xAA, 0x03, 0xFF, 0xFD, 0x06, 0x04}, {0x55, 0xAA, 0x02, 0xFF, 0xFB, 0xFB}, 7, 6, false},
        {{0x55, 0xAA, 0x1B, 0xFF, 0xFB, 0x52, 0x4D, 0x20, 0x45, 0x43, 0x34, 0x5F, 0x56, 0x31, 0x2E, 0x30, 0x30, 0x5F, 0x32, 0x30, 0x32, 0x30, 0x28, 0x32, 0x30, 0x30, 0x39, 0x33, 0x30, 0x29, 0xA5}, {0x55, 0xAA, 0x02, 0xFF, 0xFB, 0xFB}, 31, 6, false},
        {{0x55, 0xAA, 0x1B, 0xFF, 0xFB, 0x52, 0x4D, 0x20, 0x45, 0x43, 0x34, 0x5F, 0x56, 0x31, 0x2E, 0x30, 0x30, 0x5F, 0x32, 0x30, 0x32, 0x30, 0x28, 0x32, 0x30, 0x30, 0x39, 0x33, 0x30, 0x29, 0xA5}, {0x55, 0xAA, 0x02, 0x00, 0x00, 0x01}, 31, 6, false},
        {{0x55, 0xAA, 0x03, 0x40, 0x01, 0x00, 0x43}, {0x0}, 7, 1, false}
    };

    constexpr int VirtualMainboardUART::handshakeMessageResponsesCount = sizeof(handshakeMessageResponses) / sizeof(handshakeMessageResponses[0]);

    esp_err_t VirtualMainboardUART::init() {
        ESP_LOGI(TAG, "Starting VirtualMainboardUART");

        for (int i = 0; i < handshakeMessageResponsesCount; i++) {
            handshakeMessageResponses[i].sent = false;
        }

        updateLEDStateMessage(true);
        AbstractUARTYF::sendStartSequence();

        return ESP_OK;
    }

    void VirtualMainboardUART::onUARTReceive(const uint8_t* data, size_t length) {
        // no implementation, as this virtual mainboard does not receive any messages from a hardware mainboard
    }

    void VirtualMainboardUART::tickMainboardSimulationMode() {
        ESP_LOGI(TAG, "VirtualMainboardUART task started");

        while (true) {
            if (!handshakeSuccessful) {
                tryHandshake();
            }

            sendMessagesAsMainboardWouldDo();

            while(processCoverUIMessages()) {
                // Process all incoming messages
            }

            vTaskDelay(75 / portTICK_PERIOD_MS);
        }
    }

    void VirtualMainboardUART::sendMessagesAsMainboardWouldDo() {
        updateLEDStateMessage();

        // LED Status Messages
        coverUIControllerUART->sendYFMessage(currentLEDMessage);

        // Request Button states message
        const uint8_t buttonStateRequest[] = {0x55, 0xAA, 0x02, 0x50, 0x62, 0xB3};
        coverUIControllerUART->sendYFMessage(buttonStateRequest);

        if(isSecondMessage) {
            // Some status, containing lock state etc.
            const uint8_t statusMessage[] = {0x55, 0xAA, 0x05, 0x50, 0x84, 0x00, 0xFF, 0x01, 0xD8};
            coverUIControllerUART->sendYFMessage(statusMessage);
        }
        isSecondMessage = !isSecondMessage;
    }

    bool VirtualMainboardUART::processCoverUIMessages() {
        uint8_t messageBuffer[AbstractUARTConnector::MAX_MESSAGE_LENGTH] = {0};
        size_t messageLength = 0;

        if (readNextSerialMessage(messageBuffer, messageLength)) {
            // 55 AA 03 40 01 00 43 <= Handshake message from CoverUI is coming up again in times, but can be ignored
            // 55 AA 03 50 84 0D E3 <= Some status message (50 84, also comes from maiboard)
            // only show 50 00 (button release) and 50 62 button press states
            if (messageBuffer[3] == 0x50 && messageBuffer[4] == 0x00) {
                return true;    // button release confirmation
            } else if (messageBuffer[3] == 0x50 && messageBuffer[4] == 0x84) {
                return true;    // ignore for now some status message
            } else if (messageBuffer[3] == 0x40 && messageBuffer[4] == 0x01) {
                return true;    // ignore also hand shake frame ping, that comes up now and then
            } else if(messageBuffer[3] == 0x50 && messageBuffer[4] == 0x62) {
                updateButtonState(messageBuffer, messageLength);
                return true;
            }

            // Convert message to hex string for logging
            char hexMessage[AbstractUARTConnector::MAX_MESSAGE_LENGTH * 3] = {0}; // Each byte is max "FF " (3 chars)
            size_t hexIndex = 0;
            for (int i = 0; i < messageLength && hexIndex < sizeof(hexMessage) - 3; i++) {
                snprintf(&hexMessage[hexIndex], 4, "%02X ", messageBuffer[i]);
                hexIndex += 3;
            }

            ESP_LOGI("UART Received", "Unknown: %s", hexMessage);
            /*
                log of more messages found:
                55 AA 02 FF FA FA => after some kind of error, leds went off.. but on button click, at least this came.

             */

            return true;
        }

        return false;
    }

    bool VirtualMainboardUART::readNextSerialMessage(uint8_t* messageBuffer, size_t& messageLength) {
        uint8_t message[AbstractUARTConnector::MAX_MESSAGE_LENGTH] = {0};
        size_t currentLength = 0;

        uint8_t data[1];
        int length;

        while ((length = uart_read_bytes(UART_NUM_1, data, 1, 10 / portTICK_PERIOD_MS)) > 0) {
            if (currentLength == 0 && data[0] != 0x55) {
                continue; // Message does not start with 0x55
            }

            if (currentLength < AbstractUARTConnector::MAX_MESSAGE_LENGTH) {
                message[currentLength++] = data[0];

                if (AbstractUARTYF::isCompleteMessage(message, currentLength)) {
                    if (!AbstractUARTYF::hasCorrectChecksum(message, currentLength)) {
                        ESP_LOGW(TAG, "Checksum is invalid, discarding message");
                        currentLength = 0;
                        memset(message, 0, AbstractUARTConnector::MAX_MESSAGE_LENGTH);
                        continue;
                    }

                    memcpy(messageBuffer, message, currentLength);
                    messageLength = currentLength;

                    return true;
                }
            } else {
                ESP_LOGW(TAG, "Message buffer overflow!");
                return false;
            }
        }

        return false;
    }



    void VirtualMainboardUART::tryHandshake() {
        while (!handshakeSuccessful) {
            ESP_LOGI(TAG, "Trying to do handshake to CoverUI");
            processHandshake();

            if(!handshakeSuccessful) {
                ESP_LOGE(TAG, "Handshake was not successfull! Retrying in 3 seconds..");
                vTaskDelay(pdMS_TO_TICKS(3000));
            }else{
                ESP_LOGI(TAG, "Handshake was successfull!");
            }
        }
    }

    void VirtualMainboardUART::processHandshake() {
        uint8_t messageBuffer[AbstractUARTConnector::MAX_MESSAGE_LENGTH] = {0};
        size_t messageLength = 0;

        // set all response sent flags to false
        for (int i = 0; i < handshakeMessageResponsesCount; i++) {
            handshakeMessageResponses[i].sent = false;
        }

        // handshake is initialized and closed by CoverUI
        // so we react to responses of the CoverUI
        while (!handshakeSuccessful) {
            if (readNextSerialMessage(messageBuffer, messageLength)) {
                uint8_t response[AbstractUARTConnector::MAX_MESSAGE_LENGTH] = {0};
                size_t responseLength = 0;
                getHandshakeResponse(messageBuffer, messageLength, response, responseLength);

                if(responseLength == 0) {
                    if(
                        messageBuffer[0] == 0x55 && messageBuffer[1] == 0xaa &&
                        messageBuffer[3] == 0x50 && messageBuffer[4] == 0x62) {
                            ESP_LOGI(TAG, "Received button state message, means, handshake had already been done before. Lets try to boot it up!");
                            handshakeSuccessful = true;
                            return;
                    }

                    ESP_LOGW(TAG, "Received handshake message was unknown.");
                    // hexdump
                    char hexMessage[AbstractUARTConnector::MAX_MESSAGE_LENGTH * 3] = {0}; // Each byte is max "FF " (3 chars)
                    size_t hexIndex = 0;
                    for (int i = 0; i < messageLength && hexIndex < sizeof(hexMessage) - 3; i++) {
                        snprintf(&hexMessage[hexIndex], 4, "%02X ", messageBuffer[i]);
                        hexIndex += 3;
                    }
                    ESP_LOGW(TAG, "Unknown: %s", hexMessage);

                    return;  // treat handshake as failed
                }else if(responseLength == 1 && response[0] == 0x00) {
                    // this is the end message after successful handshake
                    handshakeSuccessful = true;
                    return;
                }

                sendYFMessage(response);
            }
        }

        // handshake was not successfull.. Normally, CoverUI resends the handshake messages..
        vTaskDelay(pdMS_TO_TICKS(3000));
        return;
    }

    void VirtualMainboardUART::getHandshakeResponse(const uint8_t* message, size_t length, uint8_t* responseBuffer, size_t& responseLength) {
        for (int i = 0; i < handshakeMessageResponsesCount; i++) {
            if (memcmp(message, handshakeMessageResponses[i].expectedMessage, handshakeMessageResponses[i].expectedSize) == 0) {
                if (!handshakeMessageResponses[i].sent) {
                    handshakeMessageResponses[i].sent = true;
                } else {
                    continue;
                }

                memcpy(responseBuffer, handshakeMessageResponses[i].response, handshakeMessageResponses[i].responseSize);
                responseLength = handshakeMessageResponses[i].responseSize;

                return;
            }
        }

        responseLength = 0;
    }


    void VirtualMainboardUART::updateLEDStateMessage(bool forceUpdate) {
        if (!forceUpdate && !ledState.getIsUpdated()) {
            return;
        }

        size_t messageLength = 0;
        const uint8_t* defaultMessage = boardConfig.getDefaultLEDMessage(messageLength);

        if (defaultMessage == nullptr || messageLength == 0) {
            ESP_LOGW(TAG, "No LED message available for this board.");
            return;
        }

        uint8_t newLEDMessage[AbstractUARTConnector::MAX_MESSAGE_LENGTH] = {0};
        memcpy(newLEDMessage, defaultMessage, messageLength);

        size_t ledCount;
        const auto* leds = boardConfig.getLEDConfigs(ledCount);

        for (size_t i = 0; i < ledCount; i++) {
            if (leds[i].commType == AbstractBoardConfig::CommunicationType::UART) {
                uint8_t ledStateValue = static_cast<uint8_t>(ledState.getState(static_cast<LED>(leds[i].ledIndex)));
                newLEDMessage[5 + leds[i].uartMessagePos] = ledStateValue;
            }
        }

        AbstractUARTYF::updateChecksumInMessage(newLEDMessage, messageLength);
        memcpy(currentLEDMessage, newLEDMessage, messageLength);

        ledState.setIsUpdated(false);
    }

    void VirtualMainboardUART::updateButtonState(const uint8_t* messageBuffer, size_t messageLength) {
        size_t buttonCount;
        const auto* buttons = boardConfig.getButtonConfigs(buttonCount);

        for (size_t i = 0; i < buttonCount; i++) {
            if (buttons[i].commType == AbstractBoardConfig::CommunicationType::UART) {
                if(buttons[i].uartMessagePos > messageLength - 7) {
                    ESP_LOGW(TAG, "Message length is too short for button state update: %d", messageLength);
                    return;
                }
                uint8_t buttonStateValue = messageBuffer[5 + buttons[i].uartMessagePos];
                if(buttonStateValue == 0x00) {
                    buttonState.setState(static_cast<Button>(buttons[i].buttonIndex), ButtonStateEnum::LOW, 20);
                }else if(buttonStateValue == 0x02) {
                    buttonState.setState(static_cast<Button>(buttons[i].buttonIndex), ButtonStateEnum::HIGH, 20);
                }
            }
        }
    }

    void VirtualMainboardUART::responseToHandshakeMessage(const uint8_t* message, size_t length) {
        uint8_t response[AbstractUARTConnector::MAX_MESSAGE_LENGTH] = {0};
        size_t responseLength = 0;
        getHandshakeResponse(message, length, response, responseLength);

        if(responseLength == 0) {
            if(
                message[0] == 0x55 && message[1] == 0xaa &&
                message[3] == 0x50 && message[4] == 0x62) {
                    ESP_LOGI(TAG, "Received button state message, means, handshake had already been done before. Lets try to boot it up!");
                    handshakeSuccessful = true;
                    return;
            }

            ESP_LOGW(TAG, "Received handshake message was unknown.");
            // hexdump
            char hexMessage[AbstractUARTConnector::MAX_MESSAGE_LENGTH * 3] = {0}; // Each byte is max "FF " (3 chars)
            size_t hexIndex = 0;
            for (int i = 0; i < length && hexIndex < sizeof(hexMessage) - 3; i++) {
                snprintf(&hexMessage[hexIndex], 4, "%02X ", message[i]);
                hexIndex += 3;
            }
            ESP_LOGW(TAG, "Unknown: %s", hexMessage);

            return;  // treat handshake as failed
        }else if(responseLength == 1 && response[0] == 0x00) {
            ESP_LOGI(TAG, "Handshake was successfull!");
            // this is the end message after successful handshake
            handshakeSuccessful = true;

            sendMessagesAsMainboardWouldDo();

            return;
        }

        coverUIControllerUART->sendYFMessage(response);
    }

    void VirtualMainboardUART::receiveMessageFromCoverUI(const uint8_t* data, size_t length) {
        /*
        char hexMessage[AbstractUARTConnector::MAX_MESSAGE_LENGTH * 3] = {0}; // Each byte is max "FF " (3 chars)
        size_t hexIndex = 0;
        for (int i = 0; i < length && hexIndex < sizeof(hexMessage) - 3; i++) {
            snprintf(&hexMessage[hexIndex], 4, "%02X ", data[i]);
            hexIndex += 3;
        }

        ESP_LOGI("UART Received", "Mainboard received from CoverUI: %s", hexMessage);
        */

        if(!coverUIControllerUART) {
            ESP_LOGW(TAG, "No coverUIControllerUART set for VirtualMainboardUART");
            return;
        }

        if (!handshakeSuccessful) {
            responseToHandshakeMessage(data, length);
        }else{
            addMessageToBuffer(data, length);
            processReceivedMessages();

            vTaskDelay(75 / portTICK_PERIOD_MS);
            sendMessagesAsMainboardWouldDo();
        }
    }

    void VirtualMainboardUART::addMessageToBuffer(const uint8_t* message, size_t length) {
        if (bufferLength + length > BUFFER_SIZE) {
            ESP_LOGW(TAG, "Buffer overflow, resetting received msg buffer!");
            bufferLength = 0;
        }

        memcpy(&messageBuffer[bufferLength], message, length);
        bufferLength += length;
    }

void VirtualMainboardUART::processReceivedMessages() {
    size_t i = 0;

    while (i + 2 <= bufferLength) {
        if (messageBuffer[i] == 0x55 && messageBuffer[i + 1] == 0xAA) {
            if (i + 3 > bufferLength) {
                break;
            }

            uint8_t messageLength = messageBuffer[i + 2];

            if (i + 3 + messageLength > bufferLength) {
                break;
            }

            processSingleMessage(&messageBuffer[i], messageLength + 4);

            i += messageLength + 4;
        } else {
            i++;
        }
    }

    if (i > 0 && i < bufferLength) {
        memmove(messageBuffer, &messageBuffer[i], bufferLength - i);
        bufferLength -= i;
    } else if (i >= bufferLength) {
        bufferLength = 0;
    }
}

    void VirtualMainboardUART::processSingleMessage(const uint8_t* data, size_t length) {
        // 55 AA 03 40 01 00 43 <= Handshake message from CoverUI is coming up again in times, but can be ignored
        // 55 AA 03 50 84 0D E3 <= Some status message (50 84, also comes from maiboard)
        // only show 50 00 (button release) and 50 62 button press states
        if (data[3] == 0x50 && data[4] == 0x00) {
            debugMessage(data, length);
            return;    // button release confirmation
        } else if (data[3] == 0x50 && data[4] == 0x84) {
            debugMessage(data, length);
            return;    // ignore for now some status message
        } else if (data[3] == 0x40 && data[4] == 0x01) {
            debugMessage(data, length);
            return;    // ignore also hand shake frame ping, that comes up now and then
        } else if(data[3] == 0x50 && data[4] == 0x62) {
            updateButtonState(data, length);
            return;
        }

        debugMessage(data, length);
    }

    void VirtualMainboardUART::debugMessage(const uint8_t* message, size_t length) {
        char hexMessage[AbstractUARTConnector::MAX_MESSAGE_LENGTH * 3] = {0}; // Each byte is max "FF " (3 chars)
        size_t hexIndex = 0;
        for (int i = 0; i < length && hexIndex < sizeof(hexMessage) - 3; i++) {
            snprintf(&hexMessage[hexIndex], 4, "%02X ", message[i]);
            hexIndex += 3;
        }

        ESP_LOGI("UART Received", "Message: %s", hexMessage);
    }
} // namespace YFComms

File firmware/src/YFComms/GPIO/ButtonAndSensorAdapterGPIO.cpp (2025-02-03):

#include "ButtonAndSensorAdapterGPIO.hpp"
#include <esp_log.h>

namespace YFComms {
    constexpr char TAG[] = "ButtonAndSensorAdapterGPIO";
    constexpr uint32_t DEBOUNCE_TIME_MS = 10;

    ButtonAndSensorAdapterGPIO::ButtonAndSensorAdapterGPIO(ButtonState& buttonState, const AbstractBoardConfig& boardConfig)
    : buttonState(buttonState), boardConfig(boardConfig), buttonTaskHandle(nullptr) {
        lastStateChangeTimes.fill(0);
    }

    void ButtonAndSensorAdapterGPIO::start() {
        ioExpander = I2CManager::getInstance().getIoExpander();

        if (buttonTaskHandle == nullptr) {
            xTaskCreate(buttonTask, "ButtonTask", 4096, this, 5, &buttonTaskHandle);
        }
    }

    void ButtonAndSensorAdapterGPIO::stop() {
        if (buttonTaskHandle != nullptr) {
            vTaskDelete(buttonTaskHandle);
            buttonTaskHandle = nullptr;
        }
    }

    void ButtonAndSensorAdapterGPIO::buttonTask(void* pvParameters) {
        auto* controller = static_cast<ButtonAndSensorAdapterGPIO*>(pvParameters);
        while (true) {
            controller->updateButtonStates();
            vTaskDelay(10 / portTICK_PERIOD_MS); // Task cycle interval
        }
    }

    void ButtonAndSensorAdapterGPIO::updateButtonStates() {
        uint32_t expanderStates = 0;
            esp_err_t ret = esp_io_expander_get_level(ioExpander, IO_EXPANDER_PIN_NUM_0 | IO_EXPANDER_PIN_NUM_1 | IO_EXPANDER_PIN_NUM_2 |
            IO_EXPANDER_PIN_NUM_3 | IO_EXPANDER_PIN_NUM_4 | IO_EXPANDER_PIN_NUM_5 |
            IO_EXPANDER_PIN_NUM_6 | IO_EXPANDER_PIN_NUM_7 | IO_EXPANDER_PIN_NUM_8 |
            IO_EXPANDER_PIN_NUM_9 | IO_EXPANDER_PIN_NUM_10 | IO_EXPANDER_PIN_NUM_11 |
            IO_EXPANDER_PIN_NUM_12 | IO_EXPANDER_PIN_NUM_13 | IO_EXPANDER_PIN_NUM_14, &expanderStates);
        if (ret != ESP_OK) {
            ESP_LOGW(TAG, "Failed to read Expander states: %s", esp_err_to_name(ret));
            return;
        }

        uint32_t currentTime = xTaskGetTickCount() * portTICK_PERIOD_MS;

        size_t buttonCount;
        const auto* buttons = boardConfig.getButtonConfigs(buttonCount);

        for (size_t i = 0; i < buttonCount; i++) {
            if (buttons[i].commType == AbstractBoardConfig::CommunicationType::UART) {
                continue; // UART-Buttons read on another place
            }

            // Define state by reading GPIO or Expander
            ButtonStateEnum newState = ButtonStateEnum::LOW;
            if (buttons[i].commType == AbstractBoardConfig::CommunicationType::GPIO_EXP) {
                bool isHigh = (expanderStates & buttons[i].expanderPin) != 0;
                newState = isHigh ? ButtonStateEnum::HIGH : ButtonStateEnum::LOW;
            } else if (buttons[i].commType == AbstractBoardConfig::CommunicationType::GPIO) {
                bool isHigh = gpio_get_level(static_cast<gpio_num_t>(buttons[i].gpioPin)) != 0;
                newState = isHigh ? ButtonStateEnum::HIGH : ButtonStateEnum::LOW;
            }

            // Debounce
            auto index = static_cast<size_t>(buttons[i].buttonIndex);
            uint32_t lastChangeTime = lastStateChangeTimes[index];
            uint32_t duration = currentTime - lastChangeTime;

            if (newState != buttonState.getState(static_cast<Button>(buttons[i].buttonIndex))) {
                if (newState == ButtonStateEnum::LOW && duration < 15) {
                    ESP_LOGI(TAG, "Debounced short press ignored for button %d", buttons[i].buttonIndex);
                    continue; // Ignore short releases
                }

                lastStateChangeTimes[index] = currentTime;
                buttonState.setState(static_cast<Button>(buttons[i].buttonIndex), newState, duration);
            }
        }
    }

} // namespace YFComms

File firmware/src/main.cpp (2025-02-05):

/*
 * AH20241203 infos for @patrickzzz:
 * - Quick started this test-prototype code as described in official docs
 *   https://docs.platformio.org/en/latest/tutorials/espressif32/espidf_debugging_unit_testing_analysis.html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
 *   but stopped at point 6 (Serial Monitor)
 * - Partitioned with 2*OTA "Safe update mode" see https://docs.espressif.com/projects/esp-idf/en/latest/esp32/api-reference/system/ota.html
 * - Followed Google C++ Sytle Guide see https://google.github.io/styleguide/cppguide.html#Naming except for "k" prefix for constants which I don't liked to follow ;-)
 * - Must read/best ESP-IDF reference guide https://docs.espressif.com/projects/esp-idf/en/v5.3.1/esp32s3 Awesome ESP lib, much better than Arduino!!
 * - Our currently used ESP32-S3FH4R2 also has fast 2MB (Quad SPI) PSRAM!
 *   Whenever you need some more RAM for larger (>100? byte) buffer or similar, use the PSRAM specific malloc functions to use the PSRAM (instead of heap or stack)
 */

#include <esp_log.h>
#include <freertos/FreeRTOS.h>
#include <freertos/task.h>
#include <nvs_flash.h>
#include <string.h>

#include "LedSequencer.hpp"
#include "config.h"
#include "pins.h"
#include "YFComms/CoverUIController.hpp"
#include "YFComms/State/LEDState.hpp"
#include "MyButtonHandler.hpp"
#include "mainboards/mainboard_driver_om.hpp"

static const char* TAG = "Robot Mower Interface";

// OnBoard status LEDs
LedSequencer led_grn_seq(pinLedGreen);
LedSequencer led_red_seq(pinLedRed);

// We always have one (and only one) Mainboard Device/Interface
mainboards::MainboardInterface* mainboard;

SystemHealth sys_health = {};

#define LED_SEQ_FATAL_ERROR led_red_seq.blink({.on_ms = 100, .off_ms = 100, .fulfill = true})                           // Infinite quick red LED flash
#define LED_SEQ_COMMS_ERROR led_red_seq.blink({.on_ms = 100, .off_ms = 100, .limit_blink_cycles = 1, .fulfill = true})  // One quick red flash indicate a communication error

/**
 * @brief Task which handles all LED (output?)
 *
 */
void LedsTask(void* arg) {
    while (1) {
        led_grn_seq.loop();
        led_red_seq.loop();
        vTaskDelay(ledsTaskCycle / portTICK_PERIOD_MS);
    }
}

extern "C" void app_main(void) {
    vTaskDelay(2000 / portTICK_PERIOD_MS);  // Spiritless delay for monitor. Delay depends on host PCs performance. Increase if necessary.
    ESP_LOGI(TAG, "."); // Just to get a new line in the monitor
    ESP_LOGI(TAG, "Firmware Version %d.%02d", firmwareVersion / 100, firmwareVersion % 100);

    // Initialize NVS
    // @patrickzzz Possible to use NVS instead of SPIFFS for your WiFi/WebServer?
    esp_err_t ret = nvs_flash_init();
    if (ret == ESP_ERR_NVS_NO_FREE_PAGES || ret == ESP_ERR_NVS_NEW_VERSION_FOUND) {
        ESP_LOGI(TAG, "Erase NVS flash");
        ESP_ERROR_CHECK(nvs_flash_erase());
        ret = nvs_flash_init();
    }
    ESP_ERROR_CHECK(ret);  // Abort if NVS init fails

    // Setup generic pins, which get not initialized in a separate peripheral lib
    SetupPins();

    // Create LedsTask (currently only sequencer) with a very low priority
    // This should be made as early as possible to use LED blink codes for easier visual debugging
    TaskHandle_t leds_task_handle = NULL;
    xTaskCreate(LedsTask, "LEDs_Task", 1024, NULL, 2, &leds_task_handle);

    // LED test and blink sequence indicating "Minimal setup successful"
    led_grn_seq.blink({.limit_blink_cycles = 1, .fulfill = true});  // Default = 200ms ON, 200ms OFF
    led_red_seq.blink({.limit_blink_cycles = 1, .fulfill = true});  // Default = 200ms ON, 200ms OFF

    // @patrickzzz WiFi & WebServer init should start somewhere here.
    // Mainly because WiFi doesn't depend on any of the following peripherals.
    // But backend should check for sys_health if all peripherals are healthy and report in frontend if not!
    // Example how you could fail with a mandatory peripheral (i.e. WiFi or Webserver) error
    if (esp_err_t ret = ESP_OK != ESP_OK) {  // Replace first ESP_OK with your WiFi and/or Webserver init which return with a esp_err_t
        ESP_LOGE(TAG, "Example failed with error: %s", esp_err_to_name(ret));
        LED_SEQ_FATAL_ERROR;
        return;  // Other tasks will still run!
    }

#ifdef DEV_AH
    // Example how the MainboardDriver could be used (TBD: when and where)
    // ATTENTION: Object will go into heap, but heap is limited to 4KB in ESP32 and there's no heap fragmentation protection nor heap overflow detection for most MCUs/frameworks
    mainboard = new mainboard_om::MainboardDriverOM(UART_NUM_2, pinUartOMRx, pinUartOMTx, nullptr);  // CB not implemented yet
    if (esp_err_t ret = mainboard->init() != ESP_OK) {
        ESP_LOGE(TAG, "MainboardDriverOM->init() failed with error: %s", esp_err_to_name(ret));
        led_red_seq.blink({.limit_blink_cycles = 5, .fulfill = true, .repeat = true});
        return;  // Other tasks will still run!
    }
    // This would destroy/release this mainboard instance (and will probably fragment the heap)
    // delete mainboard;
#endif
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

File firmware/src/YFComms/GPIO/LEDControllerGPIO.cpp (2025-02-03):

#include "LEDControllerGPIO.hpp"
#include <freertos/FreeRTOS.h>
#include <freertos/task.h>
#include <esp_log.h>

namespace YFComms {
    LEDControllerGPIO::LEDControllerGPIO(LEDState& ledState, const AbstractBoardConfig& boardConfig)
        : ledState(ledState), boardConfig(boardConfig), ledControllerGPIOHandle(nullptr) {
        // Initialize all LEDs to off
        turnOffAllLEDs();
    }

    void LEDControllerGPIO::start() {
        if (ledControllerGPIOHandle == nullptr) {
            xTaskCreate(ledControllerGPIOTask, "LEDControllerGPIOTask", 4096, this, 5, &ledControllerGPIOHandle);
        }
    }

    void LEDControllerGPIO::stop() {
        if (ledControllerGPIOHandle != nullptr) {
            vTaskDelete(ledControllerGPIOHandle);
            ledControllerGPIOHandle = nullptr;

            // Turn off all LEDs
            turnOffAllLEDs();
        }
    }

    void LEDControllerGPIO::ledControllerGPIOTask(void* pvParameters) {
        ESP_LOGI("LEDControllerGPIO", "Starting LEDControllerGPIOTask");
        auto* ledControllerGPIO = static_cast<LEDControllerGPIO*>(pvParameters);

        int tickCounter = 0;
        while (true) {
            ledControllerGPIO->updateLEDs(tickCounter);
            tickCounter++;

            // dont let tick counter overflow
            if (tickCounter > 1000) {
                tickCounter = 1;
            }
            vTaskDelay(50 / portTICK_PERIOD_MS); // Aktualisierung alle 50ms
        }
    }

    void LEDControllerGPIO::updateLEDs(int tickCounter) {
        size_t ledCount;
        const auto* leds = boardConfig.getLEDConfigs(ledCount);

        for (size_t i = 0; i < ledCount; i++) {
            if (leds[i].commType == AbstractBoardConfig::CommunicationType::GPIO) {
                LEDStateEnum state = ledState.getState(static_cast<LED>(leds[i].ledIndex));

                switch (state) {
                    case LEDStateEnum::ON:
                        gpio_set_level(static_cast<gpio_num_t>(leds[i].gpioPin), 1);
                        ledLastStates[leds[i].ledIndex] = 1;
                        break;

                    case LEDStateEnum::OFF:
                        gpio_set_level(static_cast<gpio_num_t>(leds[i].gpioPin), 0);
                        ledLastStates[leds[i].ledIndex] = 0;
                        break;

                    case LEDStateEnum::FLASH_SLOW:
                        if (tickCounter % 12 == 0) {
                            toggleLED(leds[i]);
                        }
                        break;

                    case LEDStateEnum::FLASH_FAST:
                        if (tickCounter % 5 == 0) {
                            toggleLED(leds[i]);
                        }
                        break;

                    default:
                        gpio_set_level(static_cast<gpio_num_t>(leds[i].gpioPin), 0);
                        ledLastStates[leds[i].ledIndex] = 0;
                        break;
                }
            }
        }
    }

    void LEDControllerGPIO::toggleLED(const AbstractBoardConfig::LEDConfig& ledConfig) {
        int currentLevel = ledLastStates[ledConfig.ledIndex];
        int newLevel = currentLevel == 0 ? 1 : 0;

        gpio_set_level(static_cast<gpio_num_t>(ledConfig.gpioPin), newLevel);
        ledLastStates[ledConfig.ledIndex] = newLevel;
    }

    void LEDControllerGPIO::turnOffAllLEDs() {
        size_t ledCount;
        const auto* leds = boardConfig.getLEDConfigs(ledCount);

        for (size_t i = 0; i < ledCount; i++) {
            if (leds[i].commType == AbstractBoardConfig::CommunicationType::GPIO) {
                gpio_set_level(static_cast<gpio_num_t>(leds[i].gpioPin), 0);
                ledLastStates[leds[i].ledIndex] = 0;
            }
        }
    }
} // namespace YFComms

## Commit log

2024-10-28 Changes to avoid watchdog timer problems: serve static files gzip compressed + increase timeout
    [main.cpp]
2024-11-11 Fix ERC issues
    [YF-Rev4-6-Adapter.kicad_sch]
2024-11-12 Add Rev4 3V3 solder jumper
    [YF-Rev4-6-Adapter.kicad_sch]
2024-11-12 Fix DRC issues
    [YF-Rev4-6-Adapter.kicad_pcb]
2024-11-12 BOM Update
    [YF-Rev4-6-Adapter.kicad_pcb, YF-Rev4-6-Adapter.kicad_sch]
2024-11-24 Add HW Prototype v0.1
    [YF-Rev4-6-Adapter.kicad_pcb, YF-Rev4-6-Adapter.kicad_sch]
2024-11-25 Change Micro-USB part to U255-051N-4BH70-SS
    [YF-Rev4-6-Adapter.kicad_pcb, YF-Rev4-6-Adapter.kicad_sch]
2024-12-04 Add test-prototype sandbox/example ESP-IDF code
    [partitions_fac_2ota_max.csv]
2024-12-04 Add HW v0.1 files and manual mods
    [YF-Rev4-6-Adapter.kicad_pcb, YF-Rev4-6-Adapter.kicad_sch, bom.csv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]
2024-12-06 Finalization of test-prototype
2024-12-27 Don't truncate logs on every startup Correct loading of mowing plan on boot up
    [logger.cpp, mower.cpp]
2024-12-28 Rev 0.2 hardware
    [MowerConnectors.kicad_sch, YF-Rev4-6-Adapter.kicad_pcb, YF-Rev4-6-Adapter.kicad_sch]
2025-01-14 Copy of test-prototype, containing a first class to speak to YF CoverUI
    [partitions_fac_2ota_max.csv]
2025-01-15 Beginning of LED State manager class
2025-01-16 Add HW comment
    [YF-Rev4-6-Adapter.kicad_sch]
2025-01-16 Add HW_0_2_X support for test-prototype
2025-01-16 Add UART pins and baud
2025-01-16 Release v0.2 prototype
    [MowerConnectors.kicad_sch, YF-Rev4-6-Adapter.kicad_pcb, YF-Rev4-6-Adapter.kicad_sch]
2025-01-18 Test for 40 Pin
2025-01-18 initial commit of protoype 2 (wip)
    [partitions_fac_2ota_max.csv]
2025-01-21 Current state, start of buttons support
2025-01-24 Branch Init and MainboardInterface PoC
    [partitions_fac_2ota_max.csv]
2025-01-24 UART read PoC, cleanup of main, complete destructors
2025-01-25 Example debugging button/hall event handler
2025-01-26 Simplified error handling in init() and derived OM driver
2025-01-27 Added button handler to main
2025-01-28 First start of uart bridge for yf
2025-01-29 Update ESP32-S3 technical reference to newer version
2025-01-30 Correction of high/low status + Beginn of UARTEventObserver Interface
2025-02-10 Prepared HW v0.3
    [MowerConnectors.kicad_sch, YF-Rev4-6-Adapter.kicad_pcb, YF-Rev4-6-Adapter.kicad_sch]
